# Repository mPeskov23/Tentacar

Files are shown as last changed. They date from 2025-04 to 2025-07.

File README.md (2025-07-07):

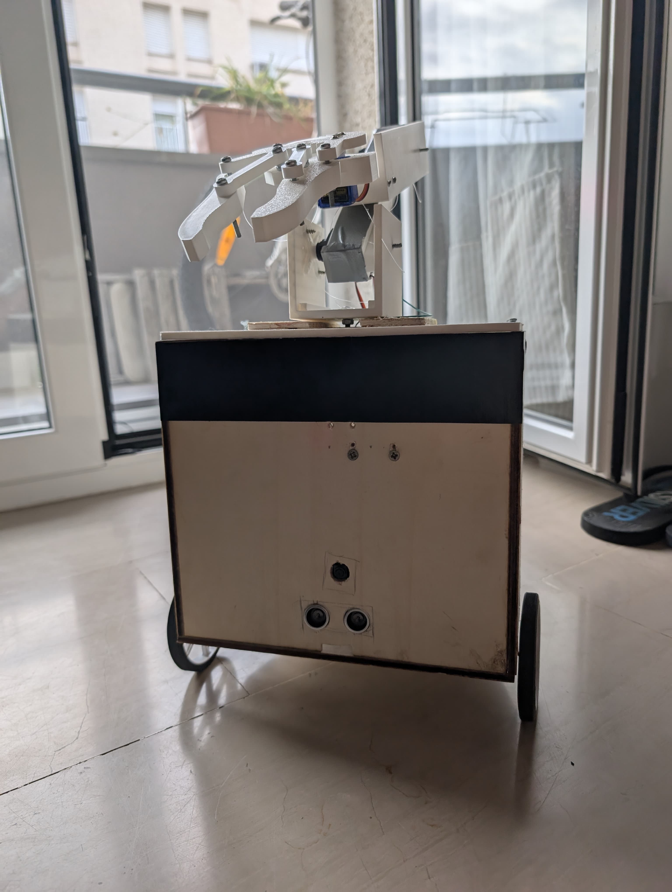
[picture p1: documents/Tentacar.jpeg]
header pic


# Tentacar Project


# Taula de Continguts
## [/3D](https://github.com/mPeskov23/Tentacar/tree/master/3D) 
Directori amb tots el models 3D utilitzats durant la creació del robot

## [/documents](https://github.com/mPeskov23/Tentacar/tree/master/documents)  

Documents necessaris per comprendre l'estructura de TentaCar, comprès per la proposta de projecte, els components del robot, el diseny del circuit i l'esquema dels móduls de software.

## [/firmware](https://github.com/mPeskov23/Tentacar/tree/master/firmware) 

Tot el codi font i recursos necessaris referent al funcionament de TentaCar. S'inclouen els móduls de control, visió i algoritmica tal que el robot pugui operar de forma autónoma.

## [/testval](https://github.com/mPeskov23/Tentacar/tree/master/testval) 

Conjunt de proves utilitzades per poder provar la funcionalitat del robot. S'ha utilitzat una simulació en un escenari controlat per tal de comprobar que totes les funcions escrites funcionen correctament.

## [/models](https://github.com/mPeskov23/Tentacar/tree/master/models)

Codi per l'utilització dels models preentrenats per la detecció d'objectes i el seu setup. 

# Qué és TentaCar?

Algún cop se us ha caigut algún objecte al terra? Clar que sí, no? I que heu fet? Us heu ajupit, l'heu agafat i heu seguit fent el que estaveu fent. 
**Però**, ara bé, i si fossiu una persona gran amb problemes a les cames que no us podeu ajupir. Qué passa si us cau el móvil o una forquilla i no el podeu agafar perque les vostres cames no responen?

Per aquest motiu, **TentaCar** és una realitat. Es tracta d'un robot amb complex de Roomba que dona voltes per la casa en busca d'algún objecte a recollir. Aquests objectes són almacenats dins el cubell que porta a sobre per poder ser agafats per l'usuari. 

# "How To Run"

Per tal de fer funcionar TentaCar és necessaria la connexió amb una rasberry pi 0 (recomanem el SO "Bullseye" per evitar els conflictes de dependències) i la seva càmera a més de les funcionalitats i llibreries necessaries per ejecutar el codi. Aquestes es troben dins del fitxer [*Requeriments.txt*](https://github.com/mPeskov23/Tentacar/blob/master/requirements.txt) o de manera més ràpida executant un [init.sh](https://github.com/mPeskov23/Tentacar/blob/master/init.sh) de la següent manera:
```bash
bash init.sh
```

# Localització d'objectes
<p>L'objectiu principal d'aquest robot és la localització dels objectes pel terra per tal de, seguidament, agafar-los i possar-los al seu darrere. Per tant la tasca principal de Tentacar recau sobre els seus ulls. Es tracta d'una càmera integrada a la Rasberry Pi 0 on a partir de la llibrería PiCamera2 i un model preeentrenat anomenat efficientdet_lite0 es poden extreure tots els objectes presents en un frame. Per tant, cada X segons, Tentacar va agafant imatges del seu voltant i les passa per un procès per tal de trobar algún objecte vàlid que pugui agafar (ja que el model detecta també objectes grans com neveres)</p>

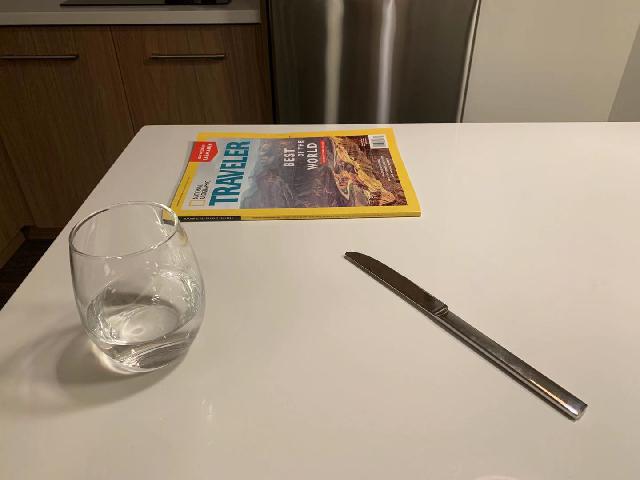
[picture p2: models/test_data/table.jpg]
  

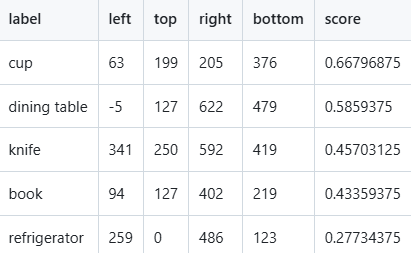
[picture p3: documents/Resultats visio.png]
  

<p>Com es pot veure en aquestes dues fotos, es detecten tots els objectes relacionats en la imatge. Però, hi ha un problema i és que les pareds no són detectades, per tan a partir d'un algorisme de contorns Canny i el càlcul del nivell de suavitat de la superficie de davant podem detectar si es tracta d'una pared o d'un objecte. Per tant, un cop tenim un objecte o pared detectats el cotxe s'ha de moure cap al seu objectiu. Quan no hi ha una pared es mou amb ajuda del sensor de proximitat controlant la orientació fent trigonometría bàsica i la distància fins a la qual s'ha de apropar. Però que passa si hi ha una pared o un pilar davant? Doncs s'utilitza bug2 algorithm, que el que fa és esquivar l'objecte intentant anar cap a la dreta d'aquest fins que trobi un camí cap endavant com en el següent exemple, on es veu un escenari extrem (ja que li em donat les coordenades del objecte, per a veure com funciona amb pareds llargues)</p>

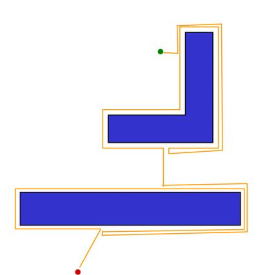
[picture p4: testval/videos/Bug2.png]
  
  

<h1> Funcionalitat de la pinça </h1>

<p>Un cop tenim l'objecte detectat i ens em situat davant, agafem un frame per tal de localitzar l'objecte en relació a la posició on possar la pinça. Més tard, es fan els càlculs d'inverse cinemàtic per possar els angles corresponents a cada servo (tenint en compte una relació 1:2 al servo de rotació) i posicionar la pinza just a sobre del objecte per seguidament tancar-la, tornar a posició inicial, girar 90 graus (relació 1:2) el servo de rotació i deixar anar l'objecte cap a dins del cubell del robot. Aquests moviments es poden veure ens els següents passos:</p>

### Pas 1

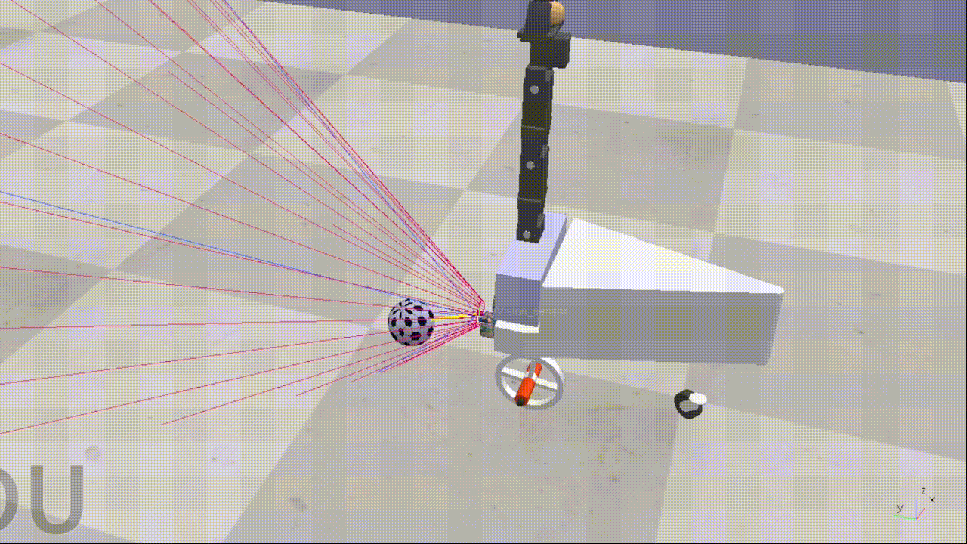
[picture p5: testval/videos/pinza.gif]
  

### Pas 2

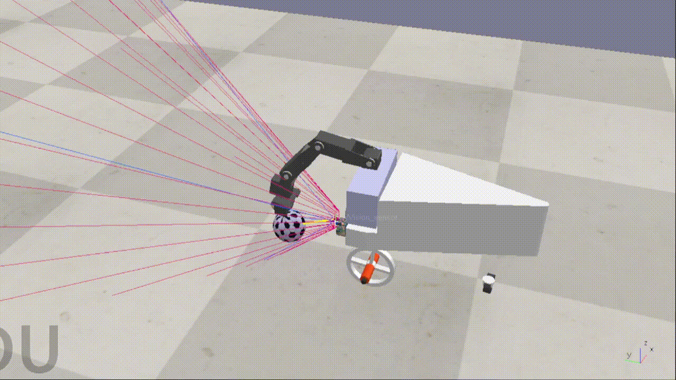
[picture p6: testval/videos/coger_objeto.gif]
  

# Social Usage

Aquest projecte està pensat per a ajudar a:
-  Persones grans o generalment a persones amb discapacitat motora que no es poden ajupir a agafar un objecte.  
- Discoteces per tal de recollir després de una llarga nit de gots pel terra, etc.. 
- Famíles amb nens a casa on normalment hi han joguines per totes bandes
- Entre d'altres...

# Autoría

Adrián Margarit 1665218 (Test Lead) 

Biel Alavedra 1666110 (HW Lead)

Mikhail Peskov 1534227 (SW Lead)

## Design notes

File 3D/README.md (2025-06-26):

# Arxius STL (3D)

En aquest directori es troben tots els models 3D utilitzats durant la creació de TentaCar. Es troba també el model 3D del tentacle, utilitzat com a objectiu principal, però degut a problemes en el projecte, s'ha hagut d'adoptar un pla de contigència per tal de canviar el tentacle per un braç pinça, localtizat també en aquest directori. 

## Móduls 3D

**3-cable SpiRob.STL:** Arxiu que conté la inspiració inicial del projecte

**tentacle_600mm.stl:** Arxiu que conté el tentacle imprés per les dimensions del nostre cotxe

**tentacar_complet.stl** Arxiu que conté el conjunt complet de forma precaria per tenir una idea del projecte final

**tentacle_complet_pinza.png:** Imatge que conté el model 3D final del cotxe i la pinça junts

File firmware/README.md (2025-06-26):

# Firmware del Robot

En aquest directori es localitza tot el codi font i recursos necessaris referent al **funcionament de TentaCar**. Aquí s'inclouen els móduls de control, visió i algoritmica tal que el robot pugui operar de forma autónoma.

## Contingut del directori

**bug2-module.py:** Algoritmica utilitzada pel moviment del robot. Es tracta d'un Bug2 Algorithm per tal de poder esquivar pareds i arribar a l'objectiu (l'objecte a agafar).

**car.py:** Control de moviment del robot .

**main.py:** Control del fluxe principal de TentaCar.

**utils_vision.py:** Crea una imatge amb les bounding boxes de la imatge agafada per la càmera de Rasberry Pi.

**vision.py:** Conté la classe de VisionModule corresponent a tota la vista del robot per tal de saber on es troben els objects, ja sigui amb un sensor de proximitat o amb la càmera per detectar si hi ha o no, objectes.

**wall_detection_module.py:** Formes de detecció de pareds per tal de poder esquivar-les i implementar bug2 algorithm correctament.

**tenta.py:** Control de la pinça del robot fent que pugui realitzar una posició "home", resetejar la posició i agafar un objecte per possar-lo al seu cistell.

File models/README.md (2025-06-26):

# Models preentrenats per visió per computador

En aquest directori es localitza tot el codi per l'utilització dels models preentrenats per la detecció d'objectes i el seu setup.
Es tracta d'un model **efficientdet_lite0.tflite** entrenat amb 80 classes per tal de detectar objectes (no inclou pareds). A més, el directori conté proves de detecció d'objectes fora de CoppeliaSim per asegurar el funcionament d'aquest.

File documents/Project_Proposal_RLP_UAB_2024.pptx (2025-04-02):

## Tentacar

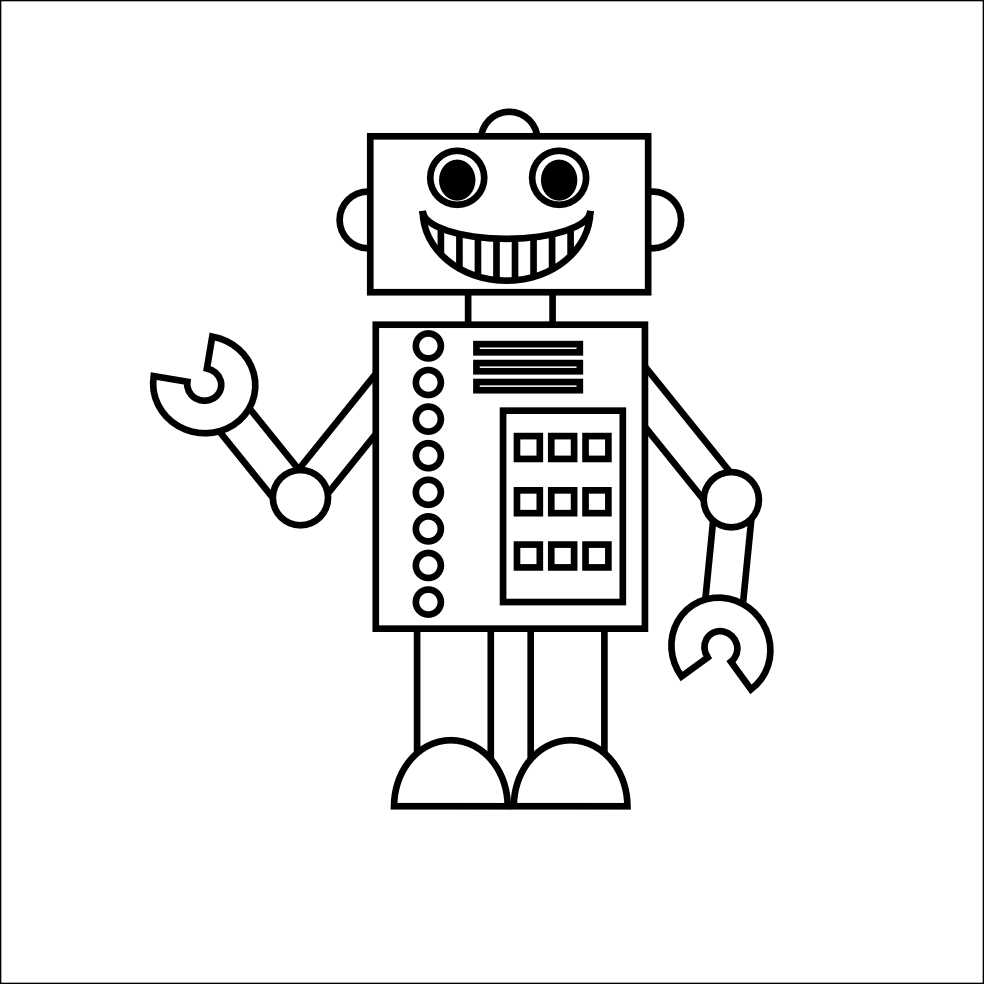
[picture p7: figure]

Tentacar es tracta d’un cotxe automàtic que té enganxat un tentacle robòtic per tal d’agafar objectes del terra, a partir d’aquí pot tenir diferents funcionalitats

AUTHORS
#Adrián Margarit 1665218 (Test Lead)

#Biel Alavedra 1666110 (SW Lead)

#Mikhail Peskov 1534227 (HW Lead)

#Lucas Aviñó 1566876 (3D lead)

ROBÒTICA, LLENGUATGE I PLANIFICACIÓ – ENGINYERIA INFORMÀTICA - UAB

## TENTACAR

Component | Units | Price/unit | Budget
TOTAL:

## Other relevant links

Internet project in which my robot is inspired

The tentacle bot (https://wyss.harvard.edu/news/the-tentacle-bot/)

Demostració tentacle (https://www.youtube.com/shorts/tXSUpIWJu00) - sobretot segon 0:42 del vídeo

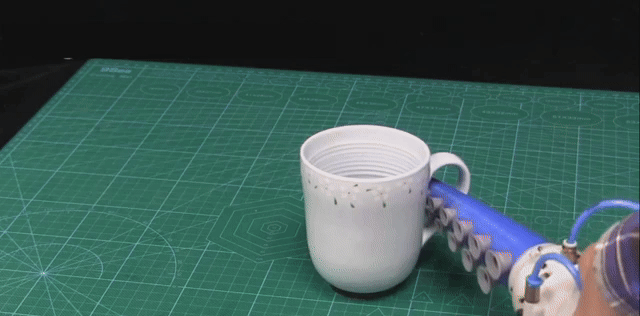
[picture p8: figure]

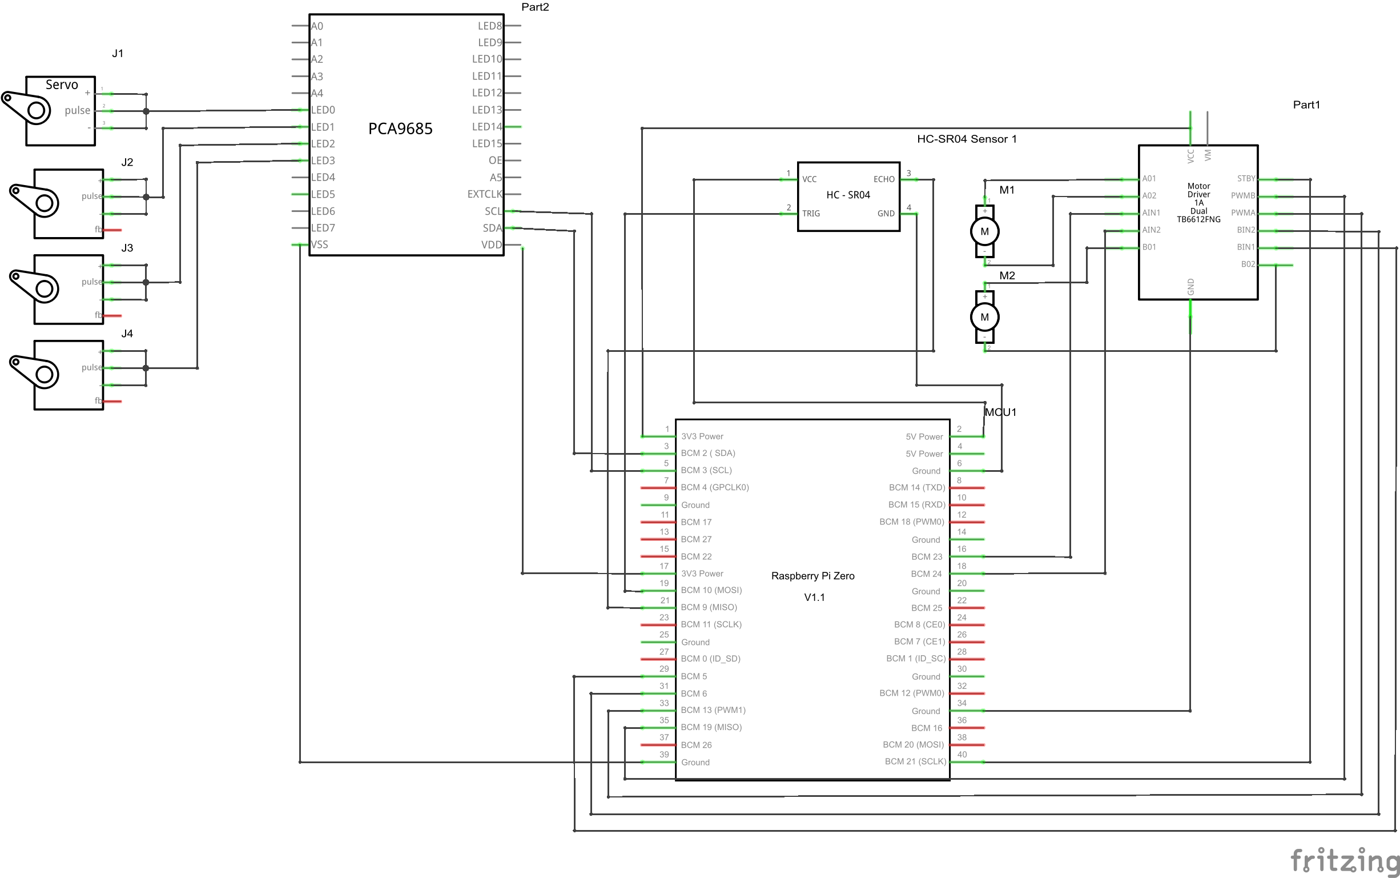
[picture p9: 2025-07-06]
documents/robot_diagram.png

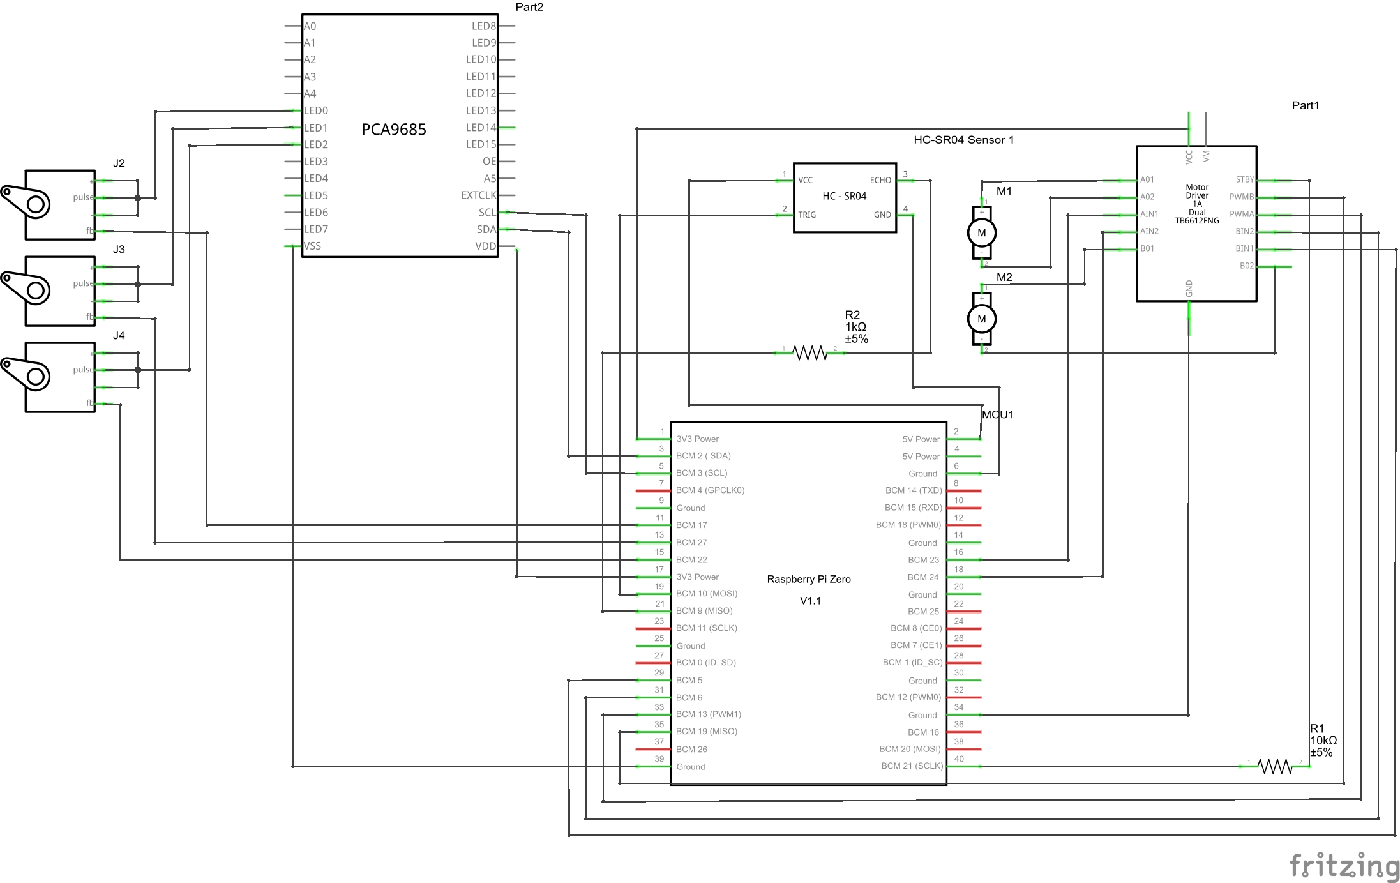
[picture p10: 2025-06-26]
documents/Esquema de Connexions.png

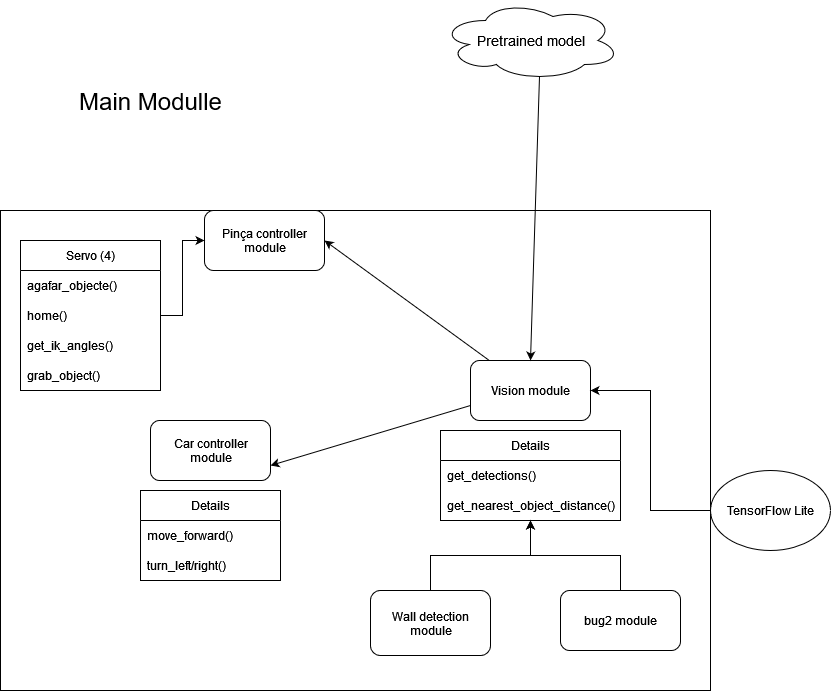
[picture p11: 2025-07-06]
documents/Esquema_Moduls_Software.png

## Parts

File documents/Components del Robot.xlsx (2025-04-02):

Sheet: Bricogeek
Name | Price | Units | Total | URL
Raspberry pi Zero v2 | €18.95 | 1.00 | 18.95 | https://tienda.bricogeek.com/placas-raspberry-pi/1996-raspberry-pi-zero-v2-wifi.html
Camera | €8.25 | 1.00 | 8.25 | https://tienda.bricogeek.com/accesorios-raspberry-pi/1472-camara-5mp-ov5647-1080p-para-raspberry-pi-zero.html
Controlador servos | €7.20 | 1.00 | 7.2 | https://tienda.bricogeek.com/controladores-motores/1764-controlador-pwm-16-canales-i2c-pca9685.html
Controlador DC | €4.95 | 1.00 | 4.95 | https://tienda.bricogeek.com/controladores-motores/999-controlador-de-motores-tb6612fng.html
Mini servo 3.5KG | €7.95 | 3.00 | 23.85 | https://tienda.bricogeek.com/servomotores/1320-mini-servo-feetech-3-5kg-ft1117m-fb-con-feedback.html
Motor DC | €4.50 | 2.00 | 9 | https://tienda.bricogeek.com/motores-dc/1833-motor-n20-con-reductora-metalica-6v-60-rpm.html
Step-down | €4.50 | 1.00 | 4.5 | https://tienda.bricogeek.com/convertidores-de-voltaje/1399-conversor-dc-dc-ajustable-5a-75w-xl4015.html
Bateria | €4.95 | 2.00 | 9.9 | https://tienda.bricogeek.com/baterias-lipo/1762-bateria-18650-recargable-2400mah-37v.html
Roadamiento | €0.95 | 1.00 | 0.95 | https://tienda.bricogeek.com/rodamientos/1294-rodamiento-608-2rs-8x22x7mm.html
TOTAL: sense IVA |  |  | 87.55
TOTAL: IVA |  |  | €105.94

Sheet: Electan
Name | Price | Units | Total | URL
TOTAL |  |  | 0

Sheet: Farnell
Name | Price | Units | Total | URL
TOTAL |  |  | 0

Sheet: Diotronic
Name | Price | Units | Total | URL
TOTAL |  |  | 0

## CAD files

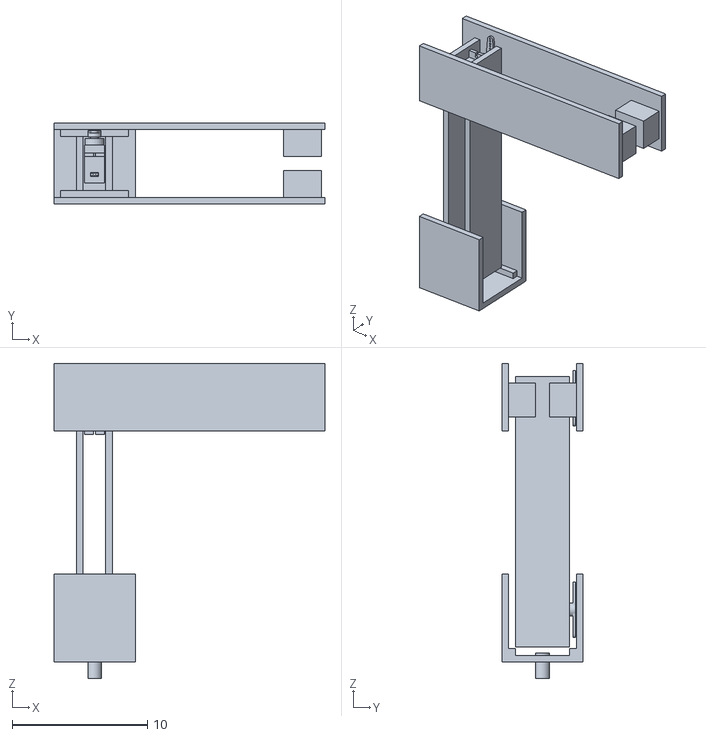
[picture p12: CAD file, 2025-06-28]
3D/Braç/braç.stl
20.0 x 6.00 x 23.3

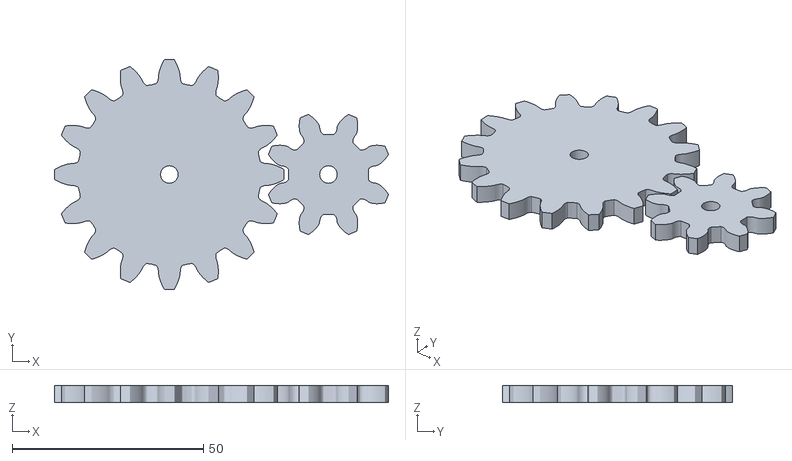
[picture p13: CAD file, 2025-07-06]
3D/Engranajes_impr.stl
87.3 x 60.0 x 4.50

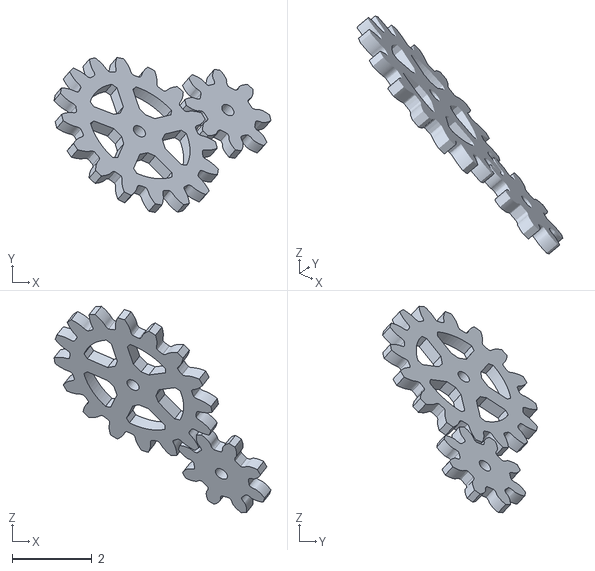
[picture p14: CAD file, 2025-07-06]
3D/Engrenage2a1.stl
5.43 x 3.88 x 5.17

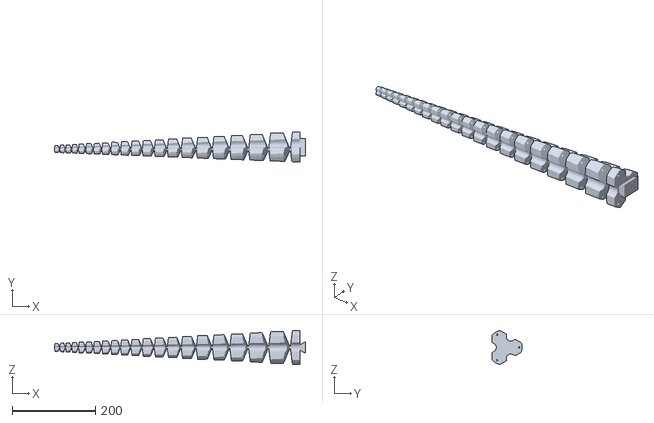
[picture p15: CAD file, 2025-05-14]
3D/tentacle_600mm.stl
603.7 x 72.4 x 82.0

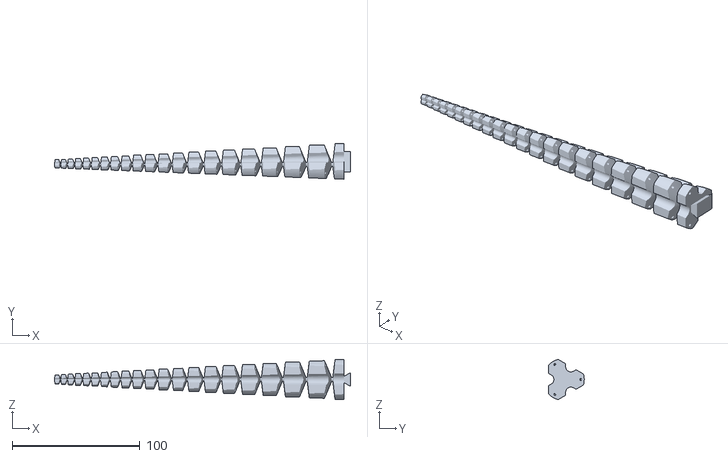
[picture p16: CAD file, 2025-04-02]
3D/3-cable SpiRob.STL
231.3 x 27.8 x 31.4

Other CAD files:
3D/Braç/braç1.skp
3D/Braç/braç2.skp
3D/Braç/braç3.skp
3D/Braç/braçTot.skp

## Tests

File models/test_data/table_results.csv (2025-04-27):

label | left | top | right | bottom | score
cup | 63 | 199 | 205 | 376 | 0.66796875
dining table | -5 | 127 | 622 | 479 | 0.5859375
knife | 341 | 250 | 592 | 419 | 0.45703125
book | 94 | 127 | 402 | 219 | 0.43359375
refrigerator | 259 | 0 | 486 | 123 | 0.27734375

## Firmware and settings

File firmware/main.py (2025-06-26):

from vision import VisionModule
from car import Car
from tenta import Tentacle
from time import time
from bug2_module import bug2

def main():
    car = Car()
    vision = VisionModule(num_threads=2)
    tentacle = Tentacle(vision)

    OBJECT_DISTANCE_THRESHOLD = 25
    SCAN_TURN_DURATION = 0.5

    try:
        while True:
            detections = vision.get_detections()
            distance = vision.get_nearest_object_distance()

            if len(detections.detections) == 0:
                car.turn_left()
                time.sleep(SCAN_TURN_DURATION)
                car.stop()
                continue

            if distance > OBJECT_DISTANCE_THRESHOLD or distance == -1:
                success = bug2(car, vision)
                if not success:
                    continue
            else:
                car.stop()
                success = tentacle.grab_object()
                if success:
                    tentacle.place_in_basket()

            time.sleep(0.1)

    except KeyboardInterrupt:
        car.stop()
        car.cleanup()

if __name__ == "main":
    main()

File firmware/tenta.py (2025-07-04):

import math
import time
import board
import busio
from adafruit_servokit import ServoKit

class Tentacle:
    def __init__(self, vision_module):
        i2c = busio.I2C(board.SCL, board.SDA)

        self.kit = ServoKit(channels=16, i2c=i2c)

        self.vision = vision_module

        self.servos = {
            'grip': self.kit.servo[0],
            'arm': self.kit.servo[1],
            'shoulder': self.kit.servo[2],
            'base': self.kit.servo[3]
        }

        self.reset()
        

    def reset(self):
        self.servos['base'].angle = 0
        time.sleep(0.1)
        self.servos['shoulder'].angle = 0
        time.sleep(0.1)
        self.servos['arm'].angle = 0
        time.sleep(0.1)
        self.servos['grip'].angle = 0
        self.base = 0
        self.shouder = 0
        self.arm = 0
        self.grip = 0
        time.sleep(0.5)

    def reset_slowly(self):
        self.smooth_move("base", self.base, 0, 2)
        time.sleep(0.1)
        self.smooth_move("shoulder", self.shoulder, 0, 2)
        time.sleep(0.1)
        self.smooth_move("arm", self.arm, 0, 2)
        time.sleep(0.1)
        self.servos['grip'].angle = 0
        self.base = 0
        self.shouder = 0
        self.arm = 0
        self.grip = 0
        time.sleep(0.5)

    def home(self):
        self.servos['base'].angle = 0
        time.sleep(0.1)
        self.servos['shoulder'].angle = 0
        time.sleep(0.1)
        self.servos['arm'].angle = 0
        self.base = 0
        self.shouder = 0
        self.arm = 0
        time.sleep(0.5)
        
        

    def get_target_coordinates(self):
        detections = self.vision.get_detections()
        if not detections or len(detections.detections) == 0:
            return None

        detection = detections.detections[0]
        bbox = detection.bounding_box
        cx = (bbox.origin_x + bbox.width / 2) / 1280
        cy = (bbox.origin_y + bbox.height / 2) / 720 
        return cx, cy
    
    def get_servo_angles_from_coords(self, cx, cy): #Primera aproximación
        base_angle = int((1.0 - cx) * 90)
        arm_angle = int((1.0 - cy) * 90)
        return base_angle, arm_angle
    
    def get_ik_angles(self, x_cm, y_cm): #Para el futuro (necesitamos todas las medidas y unas cuantas pruebas)
        L1, L2 = 20, 31 #Aquí necesitaremos las medidas reales
        dist = math.hypot(x_cm, y_cm)

        if dist > L1 + L2:
            return None

        cos_angle = (x_cm**2 + y_cm**2 - L1**2 - L2**2) / (2 * L1 * L2)
        angle2 = math.acos(cos_angle)
        k1 = L1 + L2 * math.cos(angle2)
        k2 = L2 * math.sin(angle2)
        angle1 = math.atan2(y_cm, x_cm) - math.atan2(k2, k1)

        return math.degrees(angle1), math.degrees(angle2)

    
    def grab_object(self):
        coords = self.get_target_coordinates()
        if not coords:
            return False

        cx, cy = coords
        base_angle, arm_angle = self.get_servo_angles_from_coords(cx, cy)

        self.servos['grip'].angle = 90
        time.sleep(0.5)
        self.servos['base'].angle = base_angle
        time.sleep(0.5)
        self.servos['arm'].angle = arm_angle
        time.sleep(0.5)
        self.servos['grip'].angle = 0
        time.sleep(0.5)
        self.servos['arm'].angle = 0
        time.sleep(0.5)
        self.servos['base'].angle = 180
        time.sleep(0.5)
        self.servos['grip'].angle = 90
        time.sleep(0.5)
        self.reset_position()

        return True
    
    def grab_test(self):
        self.smooth_move("base", self.base, 0)
        self.base = 0
        time.sleep(0.1)
        self.smooth_move("arm", self.arm, 30)
        self.arm = 30
        time.sleep(0.1)
        self.smooth_move("shoulder", self.shoulder, 165)
        self.shoulder = 165
        time.sleep(0.1)
        self.smooth_move("grip", self.grip, 45)
        self.grip = 45
        time.sleep(0.1)
        self.smooth_move("arm", self.arm, 90)
        self.arm = 90
        time.sleep(0.1)
        self.smooth_move("grip", self.grip, 0)
        self.grip = 45
        time.sleep(0.1)
        self.home()
        self.smooth_move("base", self.base, 90)
        self.base = 90
        self.servos["grip"].angle = 45
        self.reset_position()

    def smooth_move(self, servo_name, start, end, step = 1, delay = 0.1):
        if start > end:
            step = step * -1
        for angle in range(start, end, step):
            self.servos[servo_name].angle = angle
            print(servo_name, "has an angle ", angle)
            time.sleep(delay)

    

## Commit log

2025-04-02 Added stl model of the tentacle to /documents/parts
    [3-cable SpiRob.STL]
2025-04-15 temp_requirements.txt contains libs to headstart on windows (without camera module)
2025-04-27 Full vision module, needs on-site adjustments
    [table_results.csv]
2025-05-14 stl_tentacle_imprés
    [tentacle_600mm.stl]
2025-06-23 bug algorithm extended with obstacle detection
    [bug2_module.py]
2025-06-26 Remodel Organització Carpetes + md
    [3-cable SpiRob.STL, Cos.stl, Detector_infra_rojos.STL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]
2025-06-26 Pin map adjustments
2025-06-26 Reorganització 2
    [Components del Robot.xlsx, Cos.stl, Detector_infra_rojos.STL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]
2025-06-26 Wall detection used in bug2
    [bug2_module.py]
2025-06-28 afegir braç
    [braç.stl]
2025-06-30 more gripper tests
2025-07-01 Fitxers braç
    [braç1.skp, braç1.stl, braç2.skp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]
2025-07-04 tenta.py voltage optimization
2025-07-06 Diagrama de connexions
2025-07-06 Ficheros 3D finales y Archivos para readme
    [Engrenage2a1.stl, plac_superior_brac.stl, placa_inferior_brac.stl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]
2025-07-06 models 3d
    [Engranajes_impr.stl, braç1.stl, braç2.stl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]
2025-07-07 Reorganització Github
    [braç.stl, braç1.stl, braç2.stl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]
